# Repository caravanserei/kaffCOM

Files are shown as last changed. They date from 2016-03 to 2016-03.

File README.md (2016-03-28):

# kaffCOM
Infrared and Serial Interface for certain Swiss-made Coffeemakers.

This hardware and software is intended to read and control some coffeemakers of that well known Swiss brand (and some others) which make use of an infrared coupled diagnostic port. The same circuit can read out direct attached (plug-in) machines as well as long as they use the same TTL-based/5V UART protocol and logical interface. If the four-pin header doesn't fit your machine, maybe you find the appropriate pin-assignment of other machines and can make a simple adaptor for the relevant signals RXD, TXD and GND.

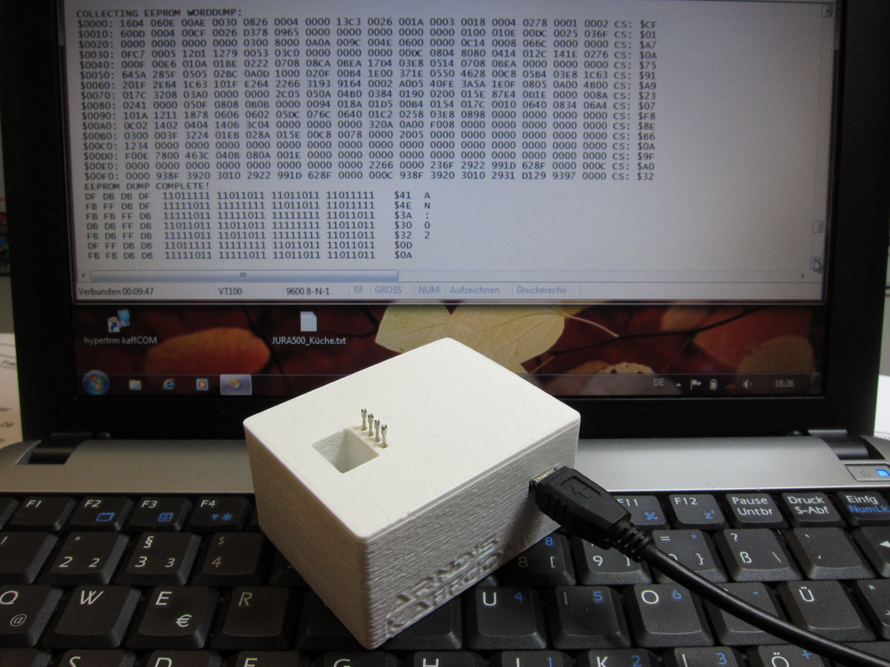
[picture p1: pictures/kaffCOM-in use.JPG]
kaffCom-at-work kaffCOM at Work!

Picture by Arnd Schaffert

kaffCOM software is based on the original Arduino-scripts "coffeemaker-communication-tool.ino" and "EEPROM_tool.ino" written by OLIVER KROHN in December 2014 which you can find on GITHUB, too: https://github.com/oliverk71/Coffeemaker-Payment-System. 

The adopted kaffCOM.ino (developed with IDE 1.6.7) is intended to be used with an Arduino NANO v3 but should work with other Arduinos, too. Be aware of low-cost NANOs from Far East with faked FTDI-chips! These are not all fakes, of course. In fact I have five well manufactured but still cheap boards with genuine chips and two least-cost boards with fakes on my bench right now. Each from different China-based sellers. Beside ORIGINAL Arduino/Genuino boards, those boards which come with a CH340G USB-device do work well, too.

You may want to build all of the electronics inlcuding the Arduino into my kaffCOM housing which is made of two self locking parts you can print with your 3D-Printer (Pretty nice previewer on GIT by now :-). When you use the infrared interface just place the box with the bigger rectangular window flat in front of the machine's infrared window: It should fit exactly into the hollow behind the keyboard hatch. When you use the pin-header for machines with a wired diagnostic interface you either may want to use spring contacts (as visible in the picture above) with crown shaped tips, or you simply make an adaptor cable with the appropriate plug on machine side and lead the three or four neccessary wires through the smaller holes. With a knot or a tie wrap on the inside as strain relief they make a fine wire guide, too and the optical section will not be hindered. The contact bars in those machines look very similar to JST XH four-pin types, but I don't know for sure.

If you are interested in the technical details please have a closer look at the not too complicated wiring diagram of kaffCOM and the pictures and oscillograms of the project.

By the way, the prototype you see here is made with the "toner-direct-method" for both the copper and the placement side.

07.03.2016 - Created this repository to share the contents.

DISCLAIMER: This project was made for fun and for private purposes only and it comes as it is without any warranty or guaranteed properties. Use at your own risk including the risk of damaging all of your devices and loss of data.

Arnd Schaffert, March 2016

Munich, Germany

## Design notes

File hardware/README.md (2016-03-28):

kaffCOM

The project's current printed circuit layout and placement scheme intended to be printed in scale 1:1.

The prototype was made with these PDFs utilizing the "toner direct method". Take care to get the correct version (mirror) as the printed side of the sheet always needs to be the side facing towards the surface with this method.

In addition you will find some oscillograms showing typical electrical signals of that very special UART-protocol.

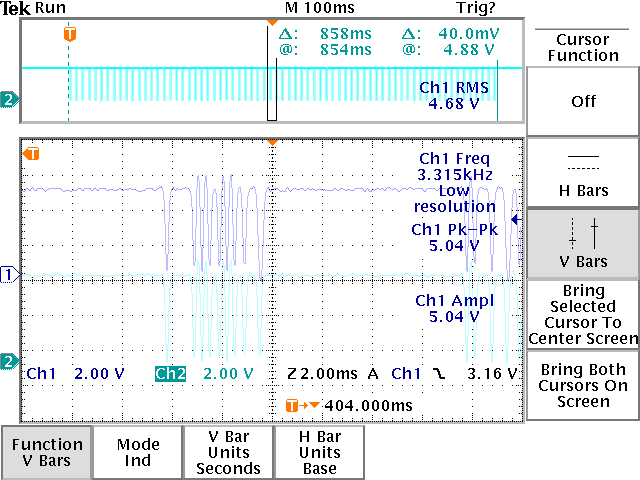
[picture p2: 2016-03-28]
hardware/answer-timing-on-RT-telegram.PNG

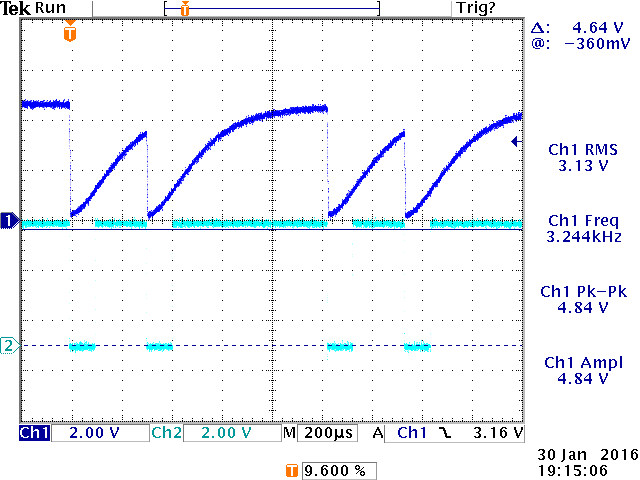
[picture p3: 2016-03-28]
hardware/TX-pulse-raw-as-received.PNG

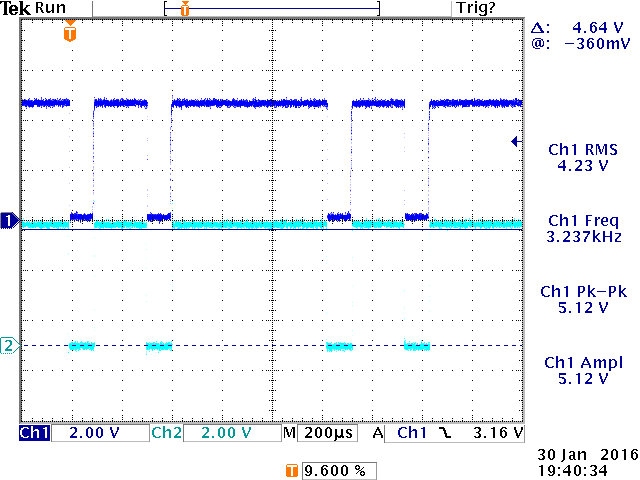
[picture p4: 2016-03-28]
hardware/TX-pulse-shaped-with-18k-resistor.PNG

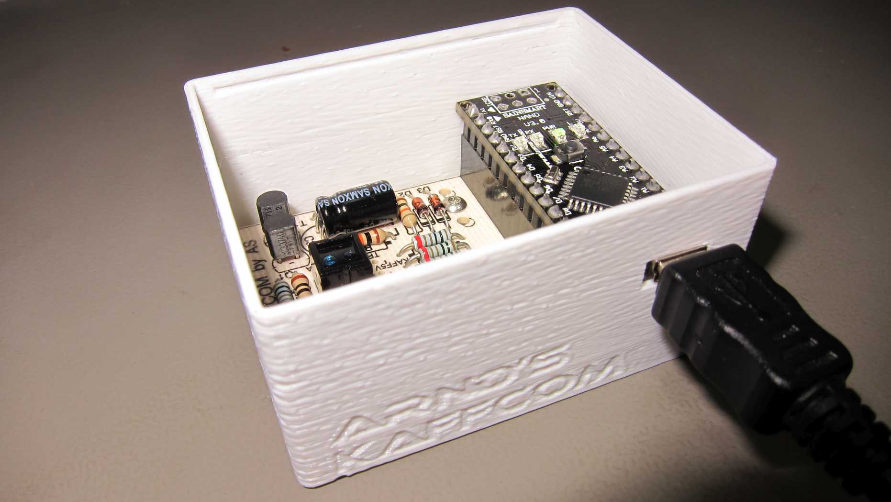
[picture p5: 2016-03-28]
kaffCOM-ready.jpg

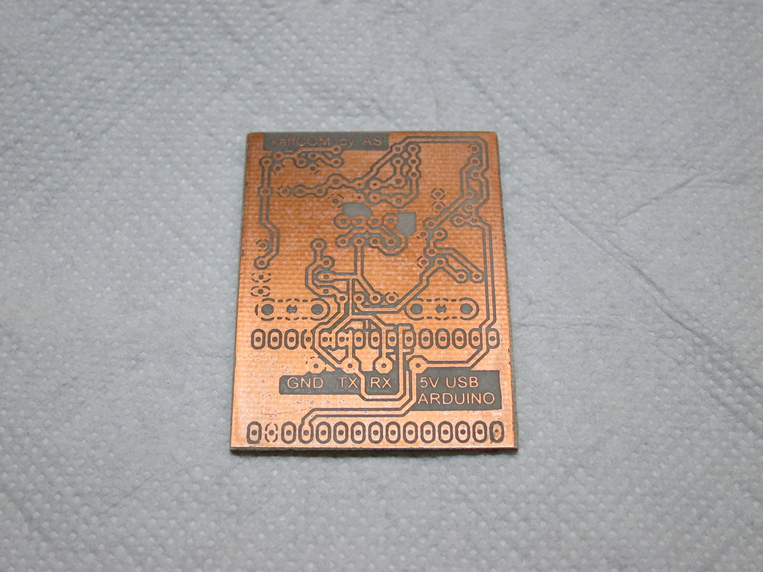
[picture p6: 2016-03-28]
pictures/kaffCOM-PCB-copper-side.JPG

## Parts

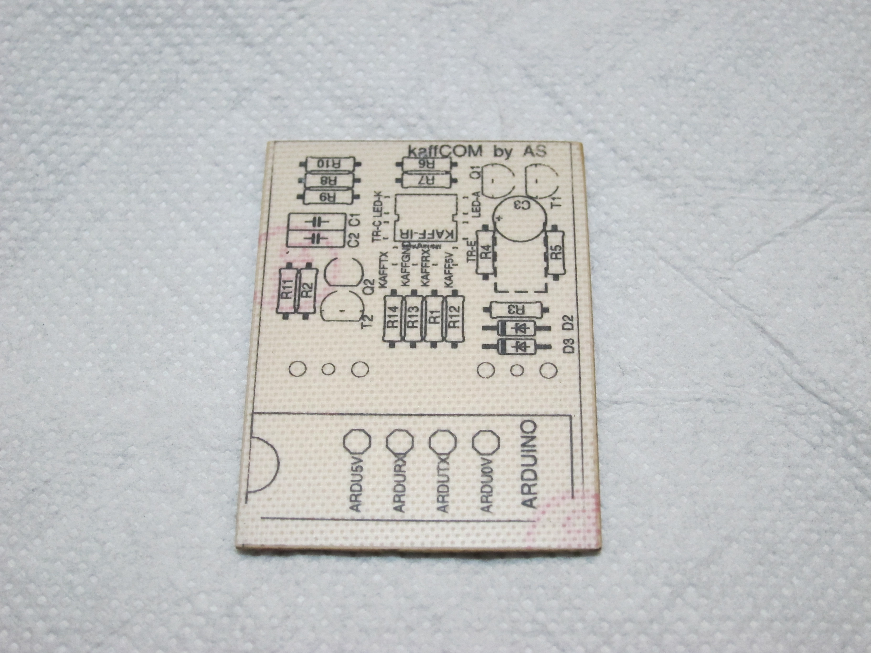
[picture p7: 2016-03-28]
pictures/kaffCOM-PCB-parts-side.JPG

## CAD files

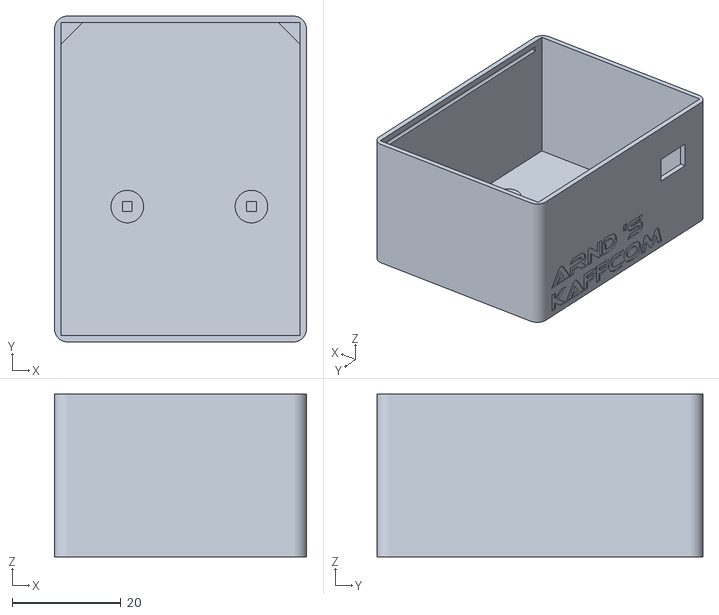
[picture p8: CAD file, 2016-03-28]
kaffCOM_housing_A_base.stl
46.4 x 60.0 x 30.0

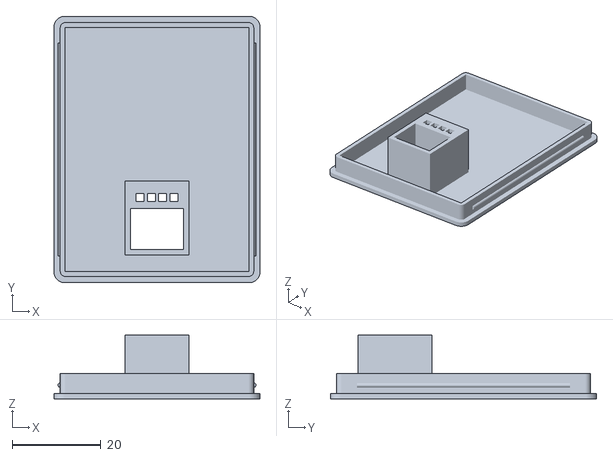
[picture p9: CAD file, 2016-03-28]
kaffCOM_housing_A_lid.stl
46.4 x 60.0 x 14.4

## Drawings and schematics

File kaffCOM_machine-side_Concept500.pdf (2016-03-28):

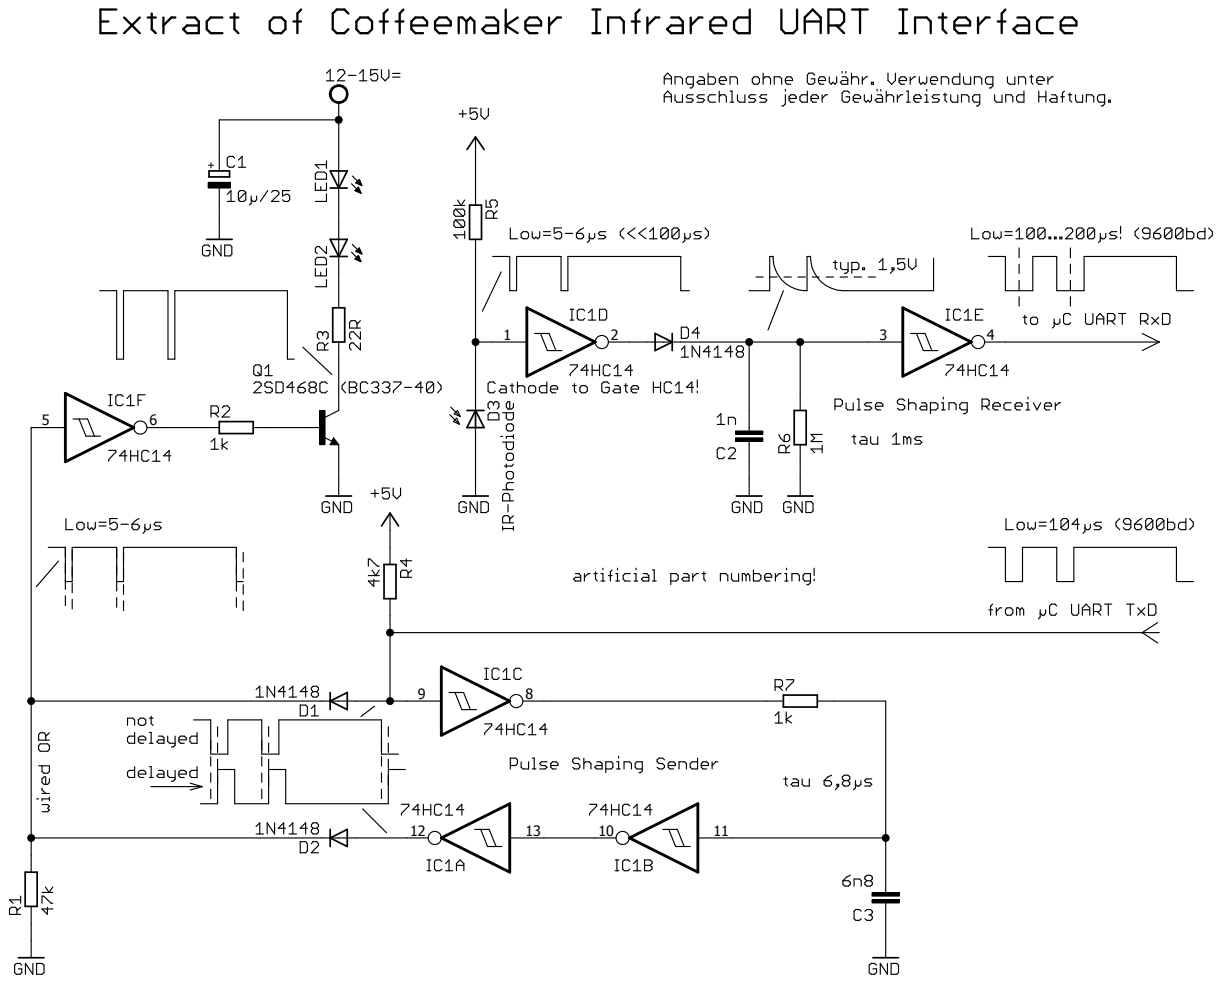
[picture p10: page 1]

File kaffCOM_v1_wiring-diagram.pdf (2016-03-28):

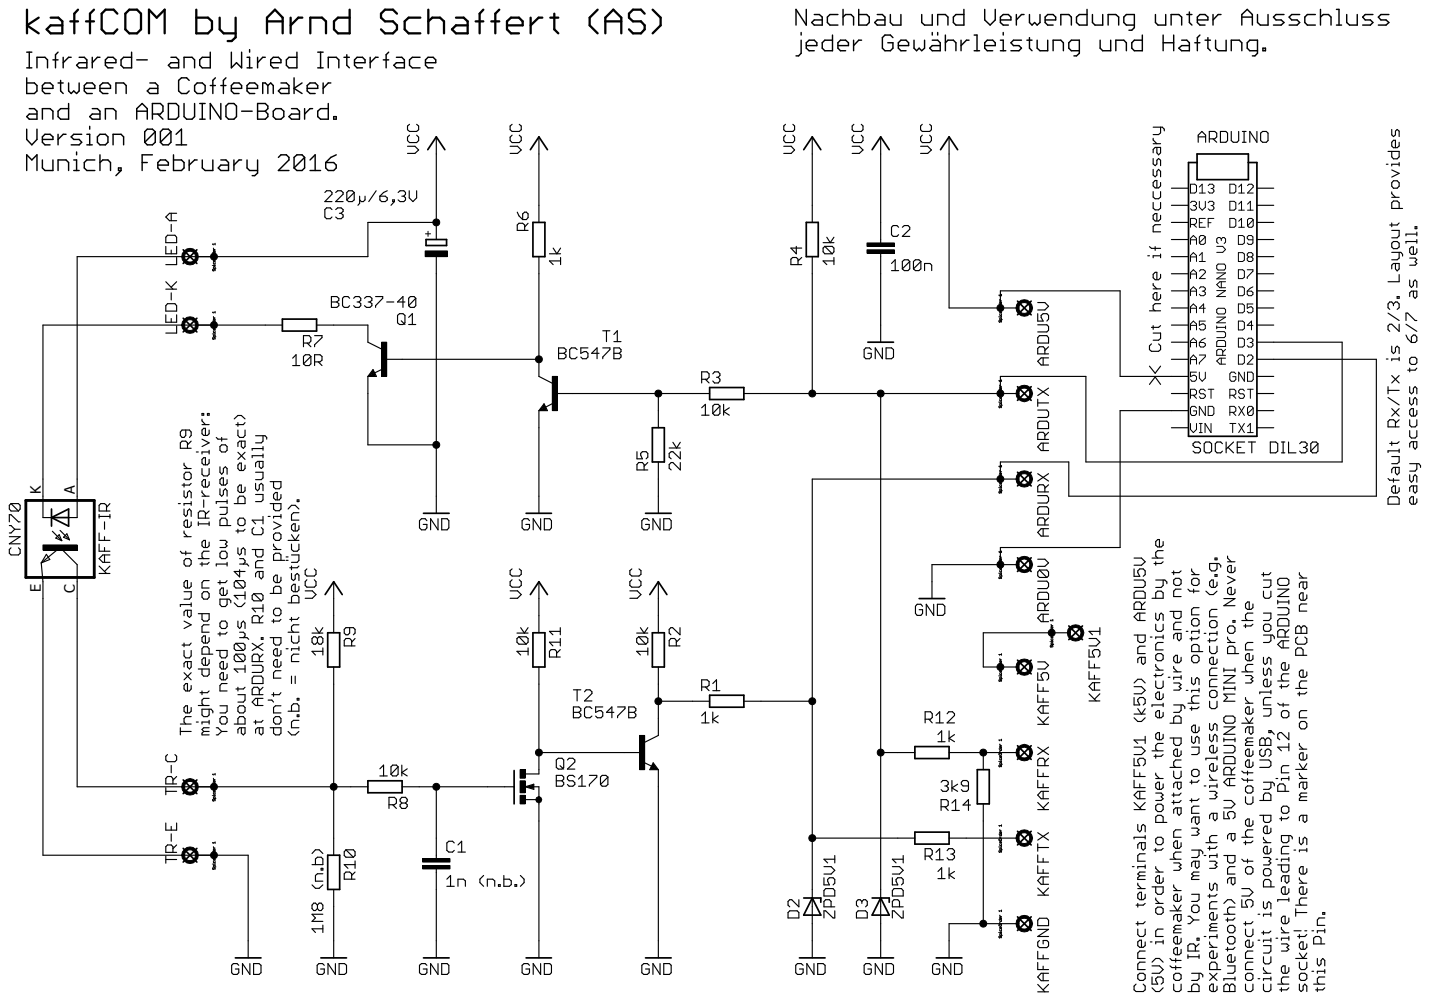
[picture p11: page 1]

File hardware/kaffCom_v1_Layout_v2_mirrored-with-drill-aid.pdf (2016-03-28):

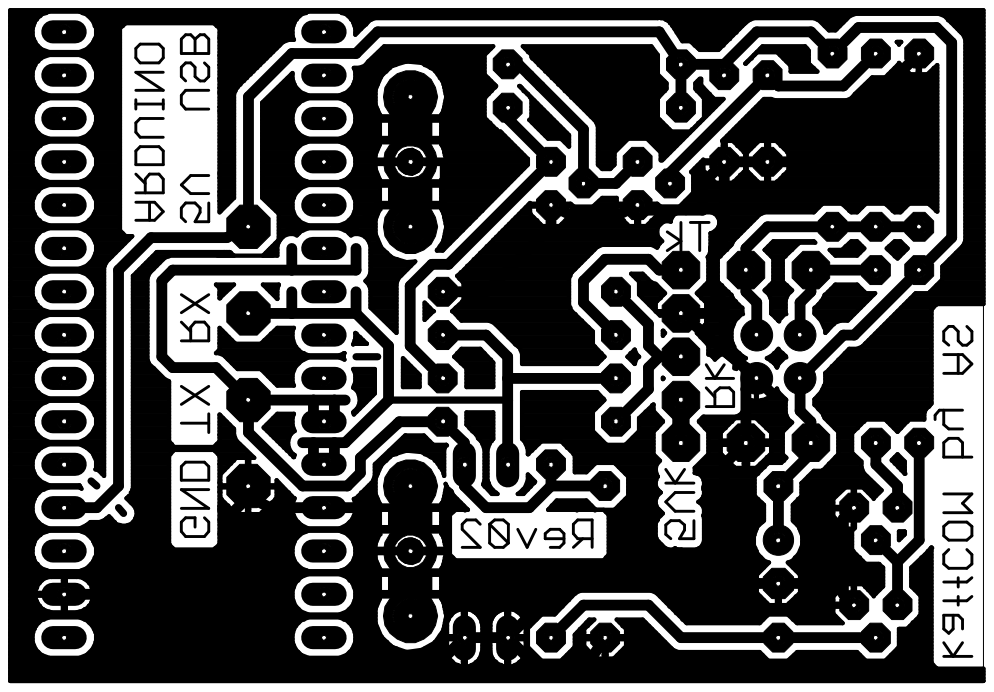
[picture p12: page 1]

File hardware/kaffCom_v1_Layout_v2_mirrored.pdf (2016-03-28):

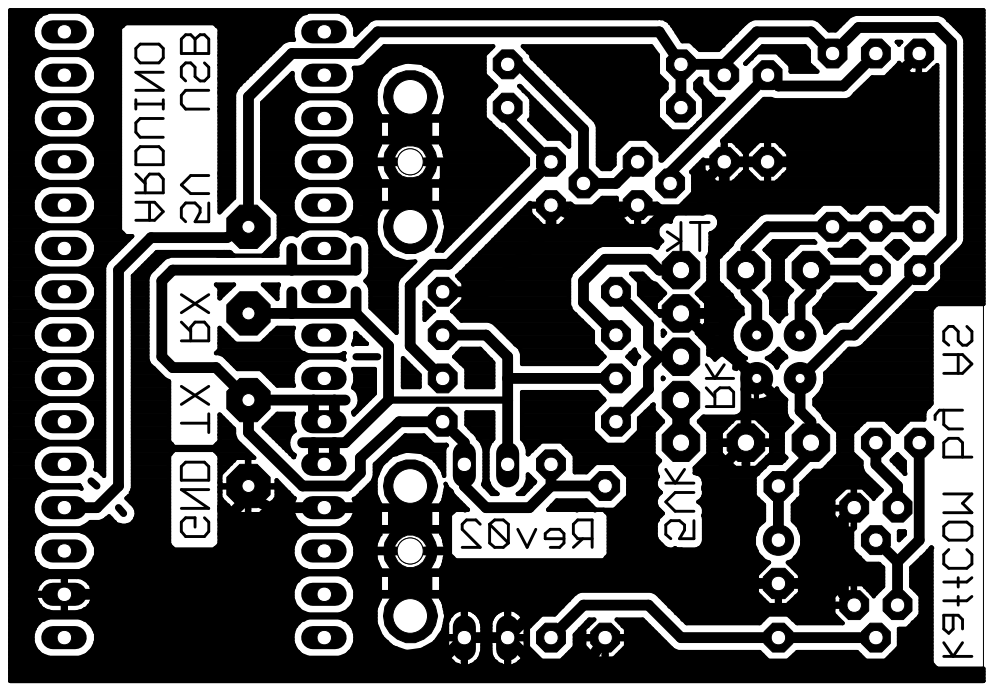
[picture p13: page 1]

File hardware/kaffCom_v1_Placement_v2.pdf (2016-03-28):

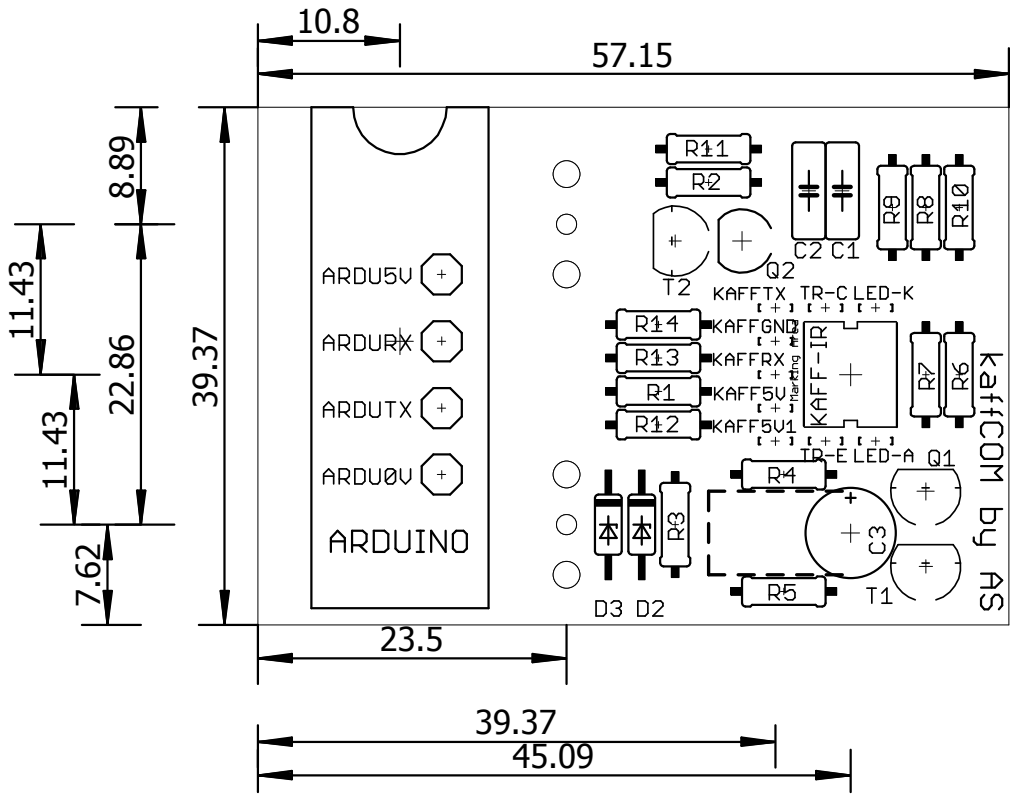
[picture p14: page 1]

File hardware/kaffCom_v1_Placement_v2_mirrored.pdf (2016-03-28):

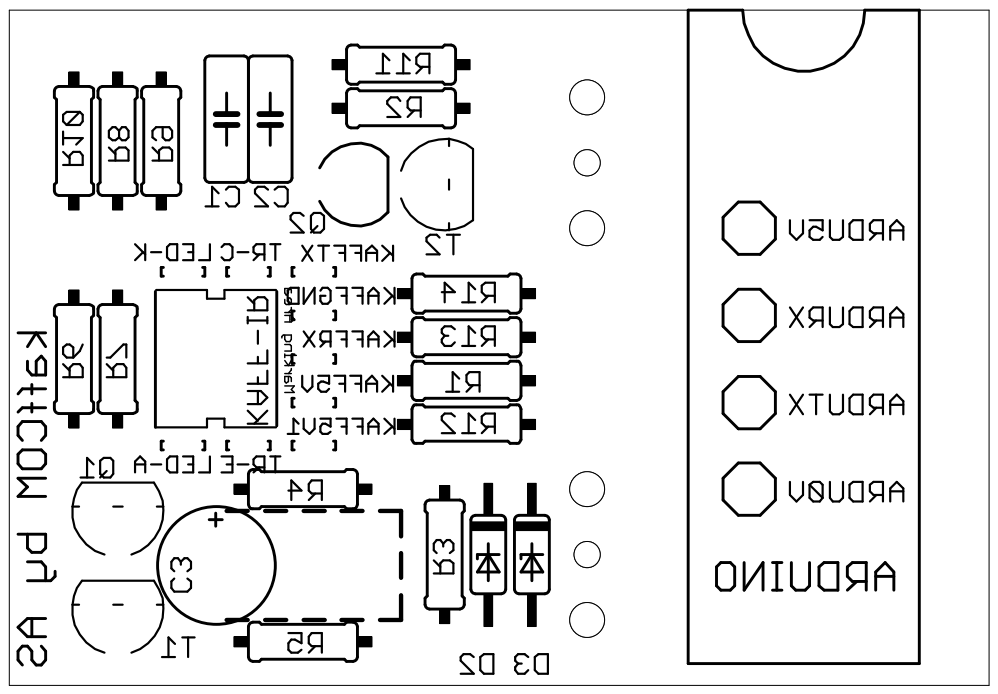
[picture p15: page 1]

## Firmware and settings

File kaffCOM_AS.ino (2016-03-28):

/* This Arduino sketch is intended for use with coffeemakers with toptronic control (e.g. my Jura Impressa S95) and allows to communicate with the coffeemaker for diagnosis, testing and modifying purposes.
  and was written in December 2014 by Oliver Krohn. Serial console should be set to include CR and NL. Hardware needed: Arduino, 4 male/female jumper wires, coffeemaker with service port.

  Additions by Arnd Schaffert (AS) in January 2016:
  - Restructured receiver section for appropriate handling of long machine response messages on 'RT:'-command.
  - A small character stand alone or preceding a regular command activates some special modes. 
  
  - Here are some regular commands (valid for Jura Impressa S90/95 only! Use at your own risk!):

  AN:01 switches coffeemaker on
  AN:02 switches coffeemaker off
  FA:04 small cup
  FA:05 two small cups
  FA:06 large cup
  FA:07 two large cups
  FA:08 steam
  FA:09 steam
  FA:0C XXL cup
  ?M1  Inkasso mode off
  ?M3  Inkasso mode on

  - Valid at least for Impressa 500/S70:
  RE:nn read word with offset 'nn' from EEPROM
  WE:nn,abcd write word 'abcd' to word-offset 'nn' into EEPROM - WARNING, may be destructive!
  RT:nn Memory dump of 16 words starting at word-offset nn (1 word = 2 byte)
  TY: shows the mask typ of main processor
  ...
  
*/

#include <SoftwareSerial.h>

SoftwareSerial mySerial(2, 3); // RX TX 
#define myBaudTx 9600

#define TRUE 1
#define FALSE 0
#define RXSIZE 512 // space for longest expected answer (RT:xx has 276 byte)
#define EESIZE 0x10 // just 16x16words for now 

byte z0;
byte z1;
byte z2;
byte z3;
byte x0;
byte x1;
byte x2;
byte x3;
byte x4;
byte intra = 1;
byte inter = 7;
byte tx2rx = 10;
const unsigned long tMaxAnswr = 1000;
byte sema = TRUE;
byte semb = TRUE;
byte semc = TRUE;
byte semd = TRUE;
byte seme = TRUE;
byte rx_array[RXSIZE];
int rx_index = 0;
int buf_index = 0;
int char_index = 0;
unsigned long timerA = 0;
int eecnt = 0;
const char assignment[]="RX/TX BITS: _--1--0--_--3--2--_--5--4--_--7--6--_";
const char commandset[]="Special Modes: c.ommand-only d.ump-512w f.ull-answer h.help Back: r.egular";
//#define assignment "RX/TX BITS: _--1--0--_--3--2--_--5--4--_--7--6--_"
//#define commandset "Special Modes: c.ommand-only d.ump-512w f.ull-answer h.help Back: r.egular"
        
void setup() {
  Serial.begin(myBaudTx);
  mySerial.begin(myBaudTx);
  rx_index = 0;
  while (rx_index < 512) rx_array[rx_index++] = 0;
  rx_index = 0;
  sema = TRUE;  //print a reminder of the bit structure once per session
  semb = FALSE; //dump mode finished  
  semc = FALSE; //command mode off
  semd = FALSE; //autodump mode off
  seme = TRUE; //regular mode on 
}

void loop() {

  if (Serial.available()) {
    if (sema == TRUE)
    {
      //print bit-assignment as a reminder once per session
      sema = FALSE;
      Serial.println("WELCOME TO kaffCOM!");
      Serial.println();
      Serial.println("Regular Mode Ready.");
      Serial.println(commandset);
      Serial.println();
    }
    
    byte c = Serial.read(); // fetch user input
    
    if ((c != 'f') && (c != 'c') && (c != 'd') && (c != 'r') && (c != 'h') && (c !='?')) //something special to do?
    {
      //no: just a regular coffeemaker-command
      toCoffeemaker(c); //send each byte immediately to CM
    }
    else
    {
      //yes: special treatment required
      if ((c == 'h') || (c == '?'))
        {
        Serial.println();  
        Serial.println(commandset);
        Serial.println(assignment);
        }
      if (c == 'r') //back to regular mode
        {
        semb = FALSE;  
        semc = FALSE;
        semd = FALSE;
        seme = TRUE;  
        Serial.println();Serial.println("REGULAR MODE READY:");
        }
      if (c == 'c') //command mode = show no answers
        {
        semb = FALSE;  
        semc = TRUE;
        semd = FALSE;
        seme = FALSE;  
        Serial.println();Serial.println("SHOW ONLY COMMANDS WITHOUT RESPONSE:");
        }
      if (c == 'f') //full mode = full interpretation of messages (this was the original function of software!)
        {
        semb = FALSE;
        semc = FALSE;
        semd = FALSE;
        seme = FALSE;  
        Serial.println();Serial.println("SHOW FULL MESSAGE INTERPRETATION:");
        Serial.println(assignment);
        }
      if (c == 'd') //get a full eeprom dump automatically
        {
        semb = TRUE; //get 1st dump immediately
        semc = TRUE; //no detailed output as in command mode
        semd = TRUE; //autodump mode ON
        seme = FALSE;
        eecnt = 0;
        Serial.println();Serial.println("COLLECTING EEPROM WORDDUMP:");
        }
    }
    RewindRxCounters(); //each character you have entered could be the last of that command, be prepared for answer!
    } // serial avail. (user input)
  
  if ((semd == TRUE) && (semb == TRUE)) // auto-generate commands for EE-auto-dump only
    {
    semb = FALSE;  
    if (eecnt < EESIZE)
      {
      byte cc;  
      if (eecnt >= 0x0A)  
        cc='A'+eecnt-0x0A;
      else
        cc='0'+eecnt;  
      toCoffeemaker('R'); 
      toCoffeemaker('T'); 
      toCoffeemaker(':');  
      toCoffeemaker(cc);  
      toCoffeemaker('0');
      toCoffeemaker('\r');
      if(eecnt>0) //strange but helpful
        toCoffeemaker('\n');
      RewindRxCounters();
      //Serial.print(" : ");  
      }
    else
      {
      //Serial.println();  
      Serial.println("EEPROM DUMP COMPLETE!");  // dump ready, return to normal mode
      semd = FALSE; 
      semc = FALSE;
      semb = FALSE;
      }
    }   
    
  // from now on simply collect bytes to be received as long there is enough buffer space
  // but do this only until the longest expected answer (currently RT: memory dump with 276 message bytes) should have been safely received
  if ((rx_index < (RXSIZE-1)) && (millis() <= (timerA + tMaxAnswr)))
  {
    if (mySerial.available()) {
      //Serial.print(rx_index);Serial.print("#");//DEBUG
      rx_array[rx_index++] = mySerial.read();
      }
  }
  else
  {
    // as the whole answer message should be received by now there is plenty of time to display it
    if (rx_index >= 19) //as of now there should have arrived 20 message-bytes with e.g "ok:<CR><LF>" at least or nothing at all
    {
      if ((semc == FALSE) && (seme == FALSE)) //show in regular mode only
      {
        Serial.print("NUMBER OF BYTES RECEIVED: "); Serial.println(rx_index);
        Serial.println(assignment);
      }
      showRxBuf(rx_index);

      
      if (semd == TRUE) // in dump mode only
        {
        semb = TRUE; // one line is done eventually
        eecnt++; // prepare next block
        }
      RewindRxCounters();
      
      }
    }

}

byte showRxBuf(int i)
{
  int k = 0;
  int cs = 0;

  byte d0; byte d1; byte d2; byte d3;
  //delay (intra); byte d0 = mySerial.read();
  //delay (intra); byte d1 = mySerial.read();
  //delay (intra); byte d2 = mySerial.read();
  //delay (intra); byte d3 = mySerial.read();
  //delay (inter);

  buf_index = 0;
  char_index = 0;
  while (buf_index < i) {
    //any four coded RX-bytes give one byte of the answer
    byte d0 = rx_array[buf_index++];
    byte d1 = rx_array[buf_index++];
    byte d2 = rx_array[buf_index++];
    byte d3 = rx_array[buf_index++];

    if ((semc == FALSE) && (seme == FALSE))
    {
      // Print hex and bin values of received UART bytes
      Serial.print(d0, HEX); Serial.print(" ");
      Serial.print(d1, HEX); Serial.print(" ");
      Serial.print(d2, HEX); Serial.print(" ");
      Serial.print(d3, HEX); Serial.print("  ");

      Serial.print(d0, BIN); Serial.print(" ");
      Serial.print(d1, BIN); Serial.print(" ");
      Serial.print(d2, BIN); Serial.print(" ");
      Serial.print(d3, BIN); Serial.print("  ");
    }

    fromCoffeemaker(d0, d1, d2, d3, char_index++);
    // additional treatment for memory dump (RT:) only:
    // characters are in buffer now (dual use) instead of the received message!
    // show a memory dump derived out of all of the received payload-characters in buffer
    // characters are in buffer now instead of received message!
    
    // get answer but don't show it in command mode
    if ((semc == TRUE) && (semd == FALSE)) break;
      
    if (buf_index == i)
    { 
      // show dump answer on explicite "rt:" answer
      if (rx_array[0] == char('r') && rx_array[1] == char('t') && rx_array[2] == char(':'))
      {
        cs = 0;
        if (semd == FALSE)
            Serial.print("WORDDUMP:");//don't know address unless in dump-mode!
          else        
            {  
            Serial.print("$0");
            if(eecnt<0x10) Serial.print("0");
            Serial.print(eecnt,HEX); Serial.print("0:");      
            }
          
        // read only the payload bytes between "rt:" and "CRLF" (dont' exceed the buffer size)
        for (k = 3; k < (RXSIZE - 1); k++)
        {
          // last two bytes must be CRLF
          if (rx_array[k] == '\r' && rx_array[k + 1] == '\n')
            break;

          // insert one space any 4 Bytes thus grouping the HEX-words
          // by the way: no need to swap bytes; take them 1:1 as they are displayed
          if ((k - 3) % 4 == 0)
          {
            Serial.print(" ");
          }
          Serial.print(char(rx_array[k]));
          // build a simple checksum on displayed characters (not on the byte/word value!) just for a quick doublecheck of the display ouptput
          cs = cs + rx_array[k];
        }
        cs = cs & 0xFF ;
        Serial.print(" CS: $");
        if (cs < 0x10) Serial.print("0");
        Serial.println(cs, HEX);
       //Serial.println();
       }//RT only
    }//end of buffer
  }//still chars to be printed 
  

}

// fromCoffeemaker receives a 4 byte UART package from the coffeemaker and translates them to a single ASCII byte
byte fromCoffeemaker(byte x0, byte x1, byte x2, byte x3, int i) {
  // Print received UART bytes on console
  //    Serial.write(x0);
  //    Serial.write(x1);
  //    Serial.write(x2);
  //    Serial.write(x3);
  //    Serial.println();
  // Reads coding Bits of the 4 byte package and writes them into a new character (translates to ASCII)
  bitWrite(x4, 0, bitRead(x0, 2));
  bitWrite(x4, 1, bitRead(x0, 5));
  bitWrite(x4, 2, bitRead(x1, 2));
  bitWrite(x4, 3, bitRead(x1, 5));
  bitWrite(x4, 4, bitRead(x2, 2));
  bitWrite(x4, 5, bitRead(x2, 5));
  bitWrite(x4, 6, bitRead(x3, 2));
  bitWrite(x4, 7, bitRead(x3, 5));
  if ((semc == FALSE) && (seme == FALSE))
  {
    // Print translated ASCII character
    Serial.print(" $");
    if (x4 < 0x10) Serial.print("0");
    Serial.print(byte(x4), HEX); Serial.print("  "); 
  }
  if(semc == FALSE)
    Serial.print(char(x4));//show interpreted answer unless in command mode
  if ((semc == FALSE) && (seme == FALSE))
  {
    Serial.println();
  }
  //use already readout buffer cells to save the translated characters for secondary use (e.g. "RT:xx" buffer-dump)
  rx_array[i] = x4;
}

// toCoffeemaker translates an ASCII character to 4 UART bytes and sends them to the coffeemaker
byte toCoffeemaker(byte zeichen)
{
  z0 = 255;
  z1 = 255;
  z2 = 255;
  z3 = 255;
  // Reads bits of ASCII byte and writes it into coding bits of 4 UART bytes
  bitWrite(z0, 2, bitRead(zeichen, 0));
  bitWrite(z0, 5, bitRead(zeichen, 1));
  bitWrite(z1, 2, bitRead(zeichen, 2));
  bitWrite(z1, 5, bitRead(zeichen, 3));
  bitWrite(z2, 2, bitRead(zeichen, 4));
  bitWrite(z2, 5, bitRead(zeichen, 5));
  bitWrite(z3, 2, bitRead(zeichen, 6));
  bitWrite(z3, 5, bitRead(zeichen, 7));

  if ((semc == FALSE) && (seme == FALSE))
  {
    // Prints hex and bin values of translated UART bytes and the source ASCII character
    Serial.print(z0, HEX); Serial.print(" ");
    Serial.print(z1, HEX); Serial.print(" ");
    Serial.print(z2, HEX); Serial.print(" ");
    Serial.print(z3, HEX); Serial.print("  ");

    Serial.print(z0, BIN); Serial.print(" ");
    Serial.print(z1, BIN); Serial.print(" ");
    Serial.print(z2, BIN); Serial.print(" ");
    Serial.print(z3, BIN); Serial.print("  ");

    Serial.print(" $");
    if (zeichen < 16) Serial.print("0");
    Serial.print(byte(zeichen), HEX); Serial.print("  ");
    Serial.write(zeichen);
    Serial.println();
  }
  else
  {
    //simply repeat each command in command mode
    if (semd == FALSE) Serial.write(zeichen);
  }
  // for each character do send a complete 4 byte coded package to the coffeemaker
  delay (intra); mySerial.write(z0);
  delay (intra); mySerial.write(z1);
  delay (intra); mySerial.write(z2);
  delay (intra); mySerial.write(z3);
  delay (inter);
  
}

void RewindRxCounters(void)
{
  timerA = millis();
  rx_index = 0;
  buf_index = 0;
  char_index = 0;
}
